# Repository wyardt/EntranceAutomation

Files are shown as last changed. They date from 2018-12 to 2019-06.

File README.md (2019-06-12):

# EntranceAutomation

This is the original use case:
### for the guest
When the guest arrives, he/she should enter the door number of the host by the keyboard and then the bell in the host's house will ring. After the identity of the visitor is confirmed using the phone of the system, the host presses the bottom and then the locked door downstairs will be open. Then the visitor can walk in.
### for the host
When the host needs to go out or come back home, he/she has to use a RF key to open the door.
### for the administator
Remote manage all the RF keys, including enable the key or disable it.

## TARGET
And my target is remake the subsystem in my house in order to control it remotely for the first step and then to make all this automatic which I don't have to 

## Detailed Needs
Below is the original goals, but it seems that it's impossible to mock the knock action from the subsystem inside the house because even though we can generate the signal which should be from the downstairs, the state of the system downstairs do will stay the same and just won't react to the unlock action from my subsystem.

~~1. Control it inside the house~~

~~* Hack the original system~~

~~* Automated open~~

~~* Automated open only once when the control switch is turned on~~

~~2. Control it from local internet web page~~

~~3. Control it from internet web page~~

~~4. Control it on my phone~~

~~5. Control it automately depending on my position~~

so here is the compromising targets:(under the scenario that somebody or I have just enter my door number and the bell is ringring)
1. Unlock the door using a single button
2. Unlock the door through my computer wirelessly
3. Unlock the door automately whoever visits
4. Unlock the door automately only once since a button has been pressed
5. Unlock the door through a web page which is post to the internet
6. Unlock the door from APP
7. Unlock the door automately depending on my position

## Hace the subsystem
First take a look at of how the system works at the normal situation. 
1. When someone enters the door number, the phone rings. If phone is picked up and unlock key is pressed, the door downstairs will be unlocked, if nobody answers, after about twenty seconds, the phone stops ringing and even then the phone is picked up and press the unlock key, there won't be any effect. So there is a time window for us to take the decision of whether unlock the door or not.
2. If nobody enters the door number, press the unlock key inside the house, there won't be any actions taken place. So we couldn't simply unlock the door downstairs whenever we want.
3. Pick up the phone inside the house, there is nothing can be heard from the line. So some mechanic blocks the voice signal when nobody visits. 

Then disassembling the subsystem[TODO image]and it turns out to be that the main chip on the subsystem is HT12D which is a serial decoder. And it could be inferred from the PCB and the frame that the top-left switch(“SW_Hook” for short below) is for the pick up action and the one(“SW_Unlock” for short below) on the right-bottom is the unlock action which is exactly the same with the print.

So here is the simplest way to hack this subsystem. On one hand, add an additional path for each of the two switches, then the control logic could be taken over by any MCU that is responsible for it. On the other hand, monitor the signal from outside the subsystem or monitor the control logic signal inside the subsystem, then the MCU could takes over the control logic inside the right time window.

So the simplest way of control the subsystem is monitor D0 and once it becomes active, enable the SW_Hook first, and then enable the SW_Unlock, so the door downstairs shall be unlocked. And more option could be added after detecting the D0 is active, such as remote notation and remote control and so on.

# More Information 
Below is the debugging and some trying with the HT12D chip which does little help of implementing the goals that mentioned. But if you are interested of the chip's function just for your information.

From datasheet of HT12D and HT12E, when someone visits, device downstairs will launch the knocking by sending:
    [sync head(12x"000" and 1x"001" )] [A0-A7][D0-D3]
which in total 13 data signals. And "001" represents '1', "011" is '0'.

For HT12D, if 3 out of 4 times of code matched, VT output high(which is not used in this subsystem), D0-D3 will be latched(D0 is used as the control signal in this subsystem), till Din is no longer active.

address set on board is 0101 1011 as it could be seen from PCB:
<div align=center>
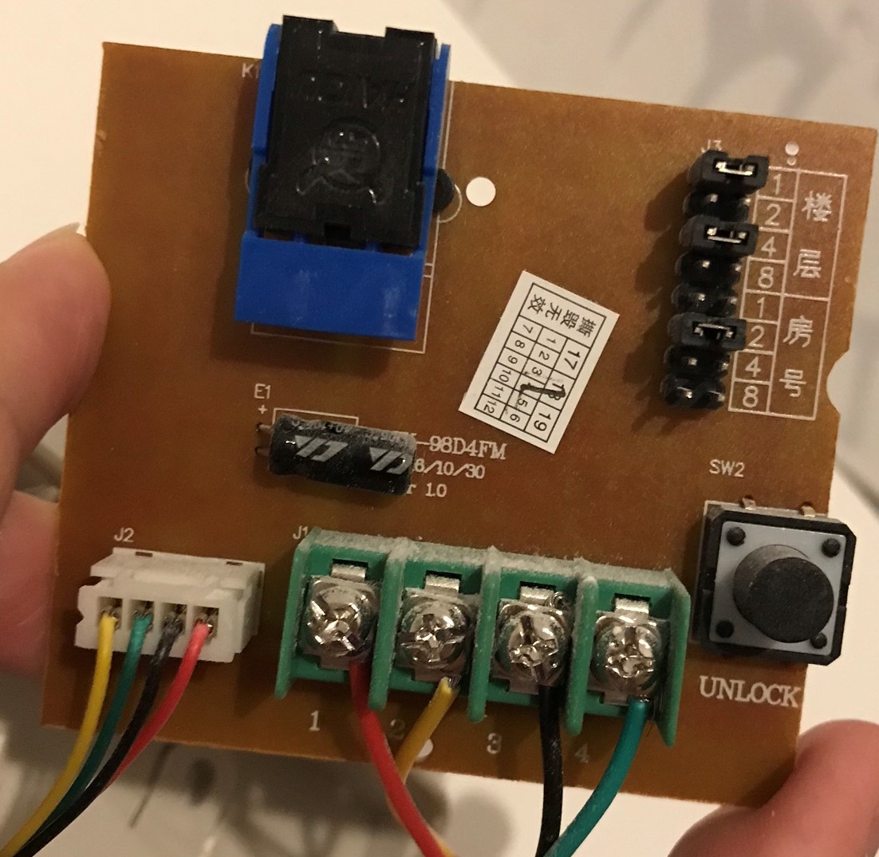
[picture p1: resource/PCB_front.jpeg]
address setting on PCB


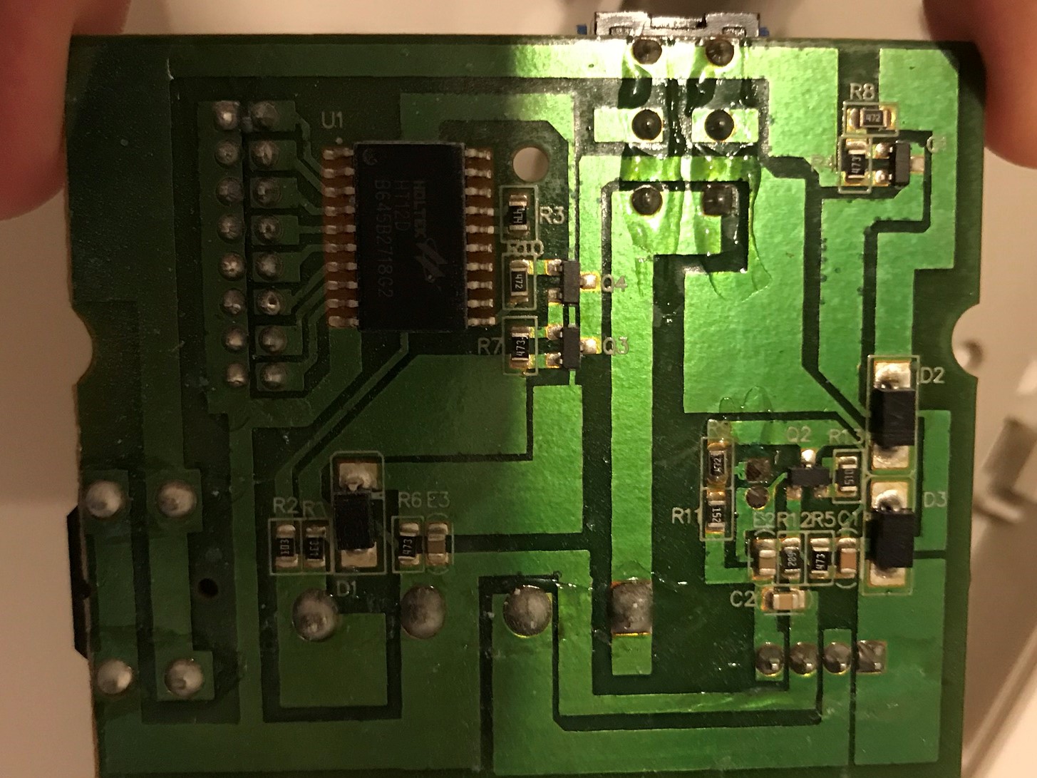
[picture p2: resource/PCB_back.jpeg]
address setting on PC

</div>

wave measured is:
1(guiding code) 0101 1011 1100 as it could be seen from oscilloscope:
<div align=center>
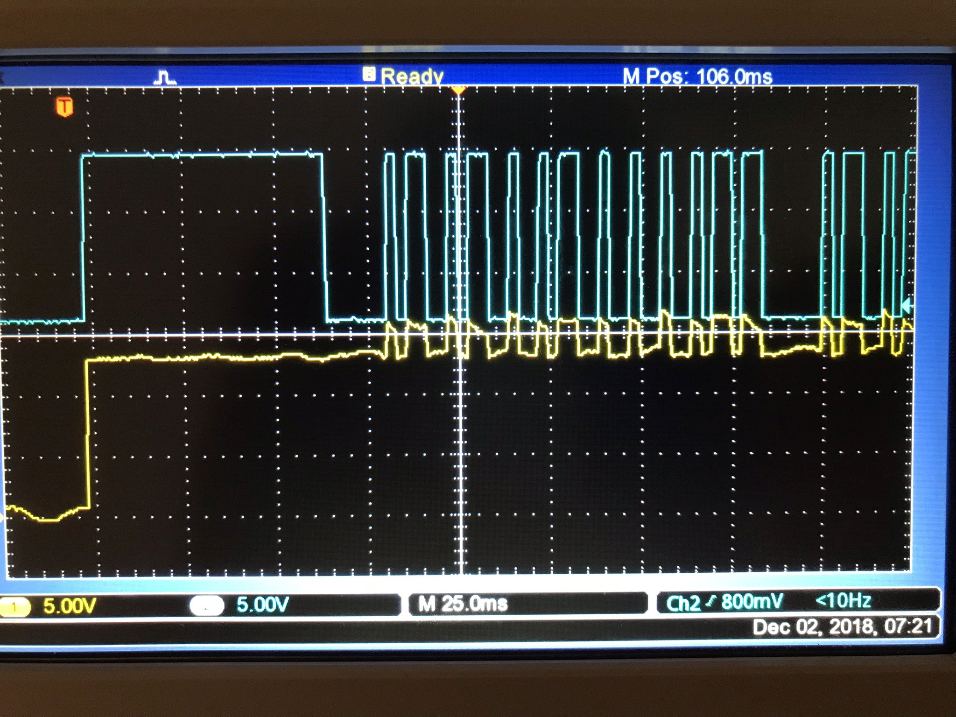
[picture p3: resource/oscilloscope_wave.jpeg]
someone knock on 502 door

</div>
and my door number is 502 so it's matched correctly.

And here is a way of decoding the knocking signal on the MCU:
record the 1.5 times the width of the sync head and use it as the mark. when the width of the upcoming signal is less than the mark, a '1' is received otherwise is a '0'.
And of course if we have another HT12D then we could emit this procedure by just monitoring the D0 signal of this HT12D chip.

# Hardware Scheme
What we have now is the subsystem itself, and we plan to take control of the two main control switches of the subsystem and what's more we don't want to modify the original functions of the subsystem, which is to say that, we could use the subsystem as what it used to be after even we have modified the subsystem by our will.

For the sake of simplicity, We choose to use modules which are off the rack. All we have to do is to redirect the control pathes onto a SPDT and use a MCU to decide which input should appear on the control path.

From the figure below it's the sketch of the modification. On the left side is the original path of the two switches, on the right side is the modification scheme.(S2 is a MUX of 2, default state is connect 3 to 2 which makes the path is the same with the original scheme)
Here we use a N-channel power MOSFET as the switch which is on when grid is positive.
<div align=center>
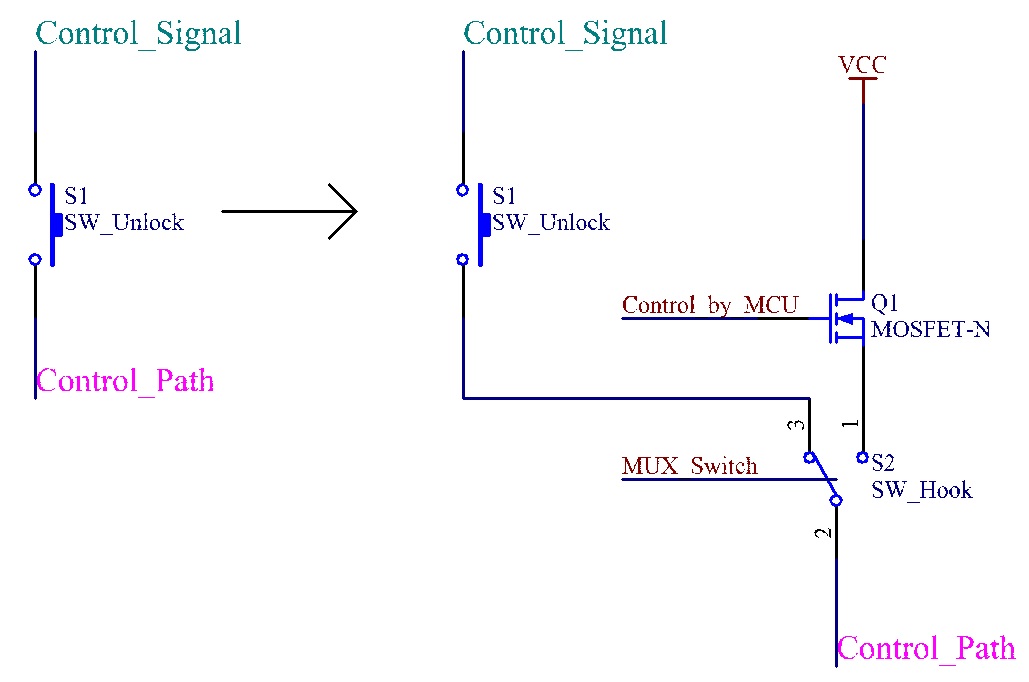
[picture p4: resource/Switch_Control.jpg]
switch_modification

</div>

Wait a minute, we have another scheme that omits the SPDT and it seems better. Look at the picture below.
<div align=center>
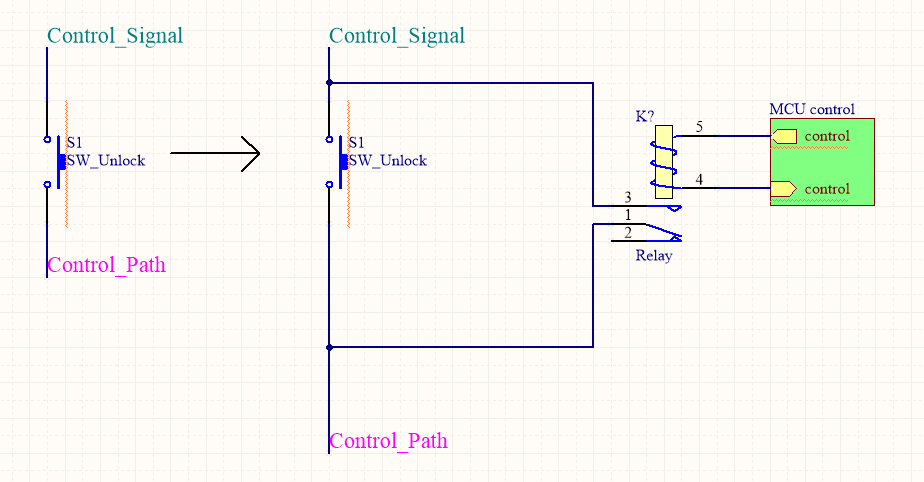
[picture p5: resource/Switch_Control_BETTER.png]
switch_modification

</div>

So this modification goes with the SW_Hook and the SW_Unlock (OR and the D0 signal path, see note below).

NOTE: for the monitor of someone visits, disconnect the D0 signal and connect it to MCU, and make the D0 signal path stay active all the time(which makes we can hear the talking all the time).(This is reserved for furthur experiment because it seems that when D0 signal path is always active, the system would be unable to function when someone enter any the door number, if this is confirmed, we can only monitor this signal and just leave it alone)

MCU we choose the STM8S103F module which is cost effective and easy to use.

What is said above are the overall modules we use with this scheme.

# Software Scheme
All we have to do is to control the MOSFET and the MUX when the D0 is detected active.
So here is the scheme of unlock the door with a single button:
1. Monitor the D0 of HT12D, if D0 is active, enable the SW_Hook control signal and go to 2, otherwise return to 1.
2. If Test Key is pressed, enable the SW_Unlock control signal and go to 3, otherwise stay in 2.
3. Wait until D0 is no longer active and go to 1, otherwise stay in 3.

Then varies functions can be deprived from the scheme above, such as control it through my computer or my mobile phone, so before all that might happen, let's build it up bit by bit.

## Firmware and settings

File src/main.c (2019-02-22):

/**
  ******************************************************************************
  * @file    Project/main.c 
  * @author  MCD Application Team
  * @version V2.1.0
  * @date    18-November-2011
  * @brief   Main program body
  ******************************************************************************
  * @attention
  *
  * THE PRESENT FIRMWARE WHICH IS FOR GUIDANCE ONLY AIMS AT PROVIDING CUSTOMERS
  * WITH CODING INFORMATION REGARDING THEIR PRODUCTS IN ORDER FOR THEM TO SAVE
  * TIME. AS A RESULT, STMICROELECTRONICS SHALL NOT BE HELD LIABLE FOR ANY
  * DIRECT, INDIRECT OR CONSEQUENTIAL DAMAGES WITH RESPECT TO ANY CLAIMS ARISING
  * FROM THE CONTENT OF SUCH FIRMWARE AND/OR THE USE MADE BY CUSTOMERS OF THE
  * CODING INFORMATION CONTAINED HEREIN IN CONNECTION WITH THEIR PRODUCTS.
  *
  * <h2><center>&copy; COPYRIGHT 2011 STMicroelectronics</center></h2>
  ******************************************************************************
  */ 


/* Includes ------------------------------------------------------------------*/
#include "stm8s.h"
#include "main.h"

bool someone_is_knocking = FALSE;
bool automate_unlock_once = FALSE;

/* Private defines -----------------------------------------------------------*/
/* Private function prototypes -----------------------------------------------*/
/* Private functions ---------------------------------------------------------*/
static void CLK_Config(void);
static void GPIO_Config(void);
static void Flash_LED(uint16_t flash_times);
static void TurnOff_LED(void);

void Delay(uint16_t nCount)
{
  /* Decrement nCount value */
  while (nCount != 0)
  {   
    nCount--;
  }
}
void main(void)
{
	disableInterrupts();

	/* Clock configuration -----------------------------------------*/
	CLK_Config();

	/* GPIO Configuration ---------------------------------------*/
  GPIO_Config();
  /* Initialize the Interrupt sensitivity */
  EXTI_SetExtIntSensitivity(EXTI_PORT_GPIOA, EXTI_SENSITIVITY_RISE_ONLY);
  EXTI_SetTLISensitivity(EXTI_TLISENSITIVITY_RISE_ONLY);
  
  enableInterrupts();

  Flash_LED(10);
  TurnOff_LED();
  wfi();
  
  while (1)
  {
  	/* if (automate_unlock_once == TRUE) */ /* under any condition */
  	{
  		automate_unlock_once = FALSE;
  		
	    if (someone_is_knocking == TRUE)
	    {
	    	Flash_LED(50);
	    	GPIO_WriteHigh(PICKUP_GPIO_PORT, PICKUP_GPIO_PINS);	/* pick up */
				Flash_LED(20);
				GPIO_WriteHigh(UNLOCK_GPIO_PORT, UNLOCK_GPIO_PINS);	/* open the gate */
				Flash_LED(20);
				GPIO_WriteLow(UNLOCK_GPIO_PORT, UNLOCK_GPIO_PINS);	/* release the button */
				Flash_LED(20);
				GPIO_WriteLow(PICKUP_GPIO_PORT, PICKUP_GPIO_PINS);	/* automate hang up */
				someone_is_knocking = FALSE;	/* open gate complete */
				Flash_LED(5);
	    }
	  }
          wfi();
  }
  
}

/**
  * @brief  Configure system clock to run at 16Mhz, default is 2MHz after reset
  * @param  None
  * @retval None
  */
static void CLK_Config(void)
{
    /* Initialization of the clock */
    /* Clock divider to HSI/1 */
    CLK_HSIPrescalerConfig(CLK_PRESCALER_HSIDIV2);
}

/**
  * @brief  Configure GPIO for buttons and Leds available on the evaluation board
  * @param  None
  * @retval None
  */
static void GPIO_Config(void)
{
  /* Initialize I/Os in Output Mode for LEDs */
	GPIO_Init(LED_GPIO_PORT, LED_GPIO_PINS, GPIO_MODE_OUT_PP_LOW_FAST);

	/* Initialize I/Os in Output Mode for control signals */
	GPIO_Init(PICKUP_GPIO_PORT, PICKUP_GPIO_PINS, GPIO_MODE_OUT_PP_LOW_FAST);
	GPIO_Init(UNLOCK_GPIO_PORT, UNLOCK_GPIO_PINS, GPIO_MODE_OUT_PP_LOW_FAST);

	/* Initialize I/Os in Input Mode for local control button */
	GPIO_Init(LOCAL_BUTTON_GPIO_PORT, LOCAL_BUTTON_GPIO_PINS, GPIO_MODE_IN_FL_IT);
	
  /* Initialize I/O in Input Mode with Interrupt for knocking signal detect */
  GPIO_Init(KNOCK_GPIO_PORT, KNOCK_GPIO_PINS, GPIO_MODE_IN_FL_IT);

	GPIO_WriteLow(PICKUP_GPIO_PORT, PICKUP_GPIO_PINS);	/* default state is hooked */
  GPIO_WriteLow(UNLOCK_GPIO_PORT, UNLOCK_GPIO_PINS);	/* default is no action to open the gate */
}

/**
  * @brief  Flash the LED to indicate process is run here
  * @param  None
  * @retval None
  */
static void Flash_LED(uint16_t flash_times)
{
  uint16_t i;
	/* LED flashes to indicate successful initiation */
  for (i = 0; i < flash_times; i++)
  {
		GPIO_WriteReverse(LED_GPIO_PORT, LED_GPIO_PINS);
		Delay(0xffff);
  }

}

/**
  * @brief  Turn off the LED
  * @param  None
  * @retval None
  */
static void TurnOff_LED(void)
{
	GPIO_WriteHigh(LED_GPIO_PORT, LED_GPIO_PINS);
}

#ifdef USE_FULL_ASSERT

/**
  * @brief  Reports the name of the source file and the source line number
  *   where the assert_param error has occurred.
  * @param file: pointer to the source file name
  * @param line: assert_param error line source number
  * @retval : None
  */
void assert_failed(u8* file, u32 line)
{ 
  /* User can add his own implementation to report the file name and line number,
     ex: printf("Wrong parameters value: file %s on line %d\r\n", file, line) */

  /* Infinite loop */
  while (1)
  {
  }
}
#endif

/******************* (C) COPYRIGHT 2011 STMicroelectronics *****END OF FILE****/

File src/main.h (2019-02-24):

/**
  ******************************************************************************
  * @file    EXTI_InterruptPriority\main.h
  * @author  MCD Application Team
  * @version V2.0.4
  * @date    26-April-2018
  * @brief   This file contains the external declaration for main.c file.
  ******************************************************************************
  * @attention
  *
  * <h2><center>&copy; COPYRIGHT 2014 STMicroelectronics</center></h2>
  *
  * Licensed under MCD-ST Liberty SW License Agreement V2, (the "License");
  * You may not use this file except in compliance with the License.
  * You may obtain a copy of the License at:
  *
  *        http://www.st.com/software_license_agreement_liberty_v2
  *
  * Unless required by applicable law or agreed to in writing, software 
  * distributed under the License is distributed on an "AS IS" BASIS, 
  * WITHOUT WARRANTIES OR CONDITIONS OF ANY KIND, either express or implied.
  * See the License for the specific language governing permissions and
  * limitations under the License.
  *
  ******************************************************************************
  */   

/* Define to prevent recursive inclusion -------------------------------------*/
#ifndef __MAIN_H
#define __MAIN_H

/* Private typedef -----------------------------------------------------------*/
/* Private define ------------------------------------------------------------*/
#define LED_GPIO_PORT  (GPIOB)
#define LED_GPIO_PINS  (GPIO_PIN_5)
#define KNOCK_GPIO_PORT  (GPIOA)
#define KNOCK_GPIO_PINS  (GPIO_PIN_1)
#define PICKUP_GPIO_PORT  (GPIOA)
#define PICKUP_GPIO_PINS  (GPIO_PIN_2)
#define UNLOCK_GPIO_PORT  (GPIOD)
#define UNLOCK_GPIO_PINS  (GPIO_PIN_4)
#define LOCAL_BUTTON_GPIO_PORT  (GPIOD)
#define LOCAL_BUTTON_GPIO_PINS  (GPIO_PIN_5)



/* Private function prototypes -----------------------------------------------*/
/* Private functions ---------------------------------------------------------*/

/* Public functions ----------------------------------------------------------*/
extern bool someone_is_knocking;
extern bool automate_unlock_once;

#endif /* __MAIN_H */


/************************ (C) COPYRIGHT STMicroelectronics *****END OF FILE****/

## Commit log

2018-12-10 add Switch Control sketch
2018-12-11 Add AD scheme of switch path upgrade
    [Switch_Control.SchDoc]
2018-12-11 Modify Switch_Control.jpg
2018-12-11 add gitignore and move AD files to resource folder
    [Switch_Control.SchDoc]
2018-12-15 Use a better scheme of switch control side path
    [Switch_Control.SchDoc]
2019-01-20 add en.stsw-stm8069.zip which contains the stm8s10x standard peripheral driver
2019-01-23 use "!= RESET" instead of "== SET" when determine interrupt IOs
    [main.c, main.h, stm8s_it.c]
2019-02-16 switch pickup key and unlock key add delay before pickup succeed of automate unlock the gate
2019-02-22 modify the better hardware scheme
    [Switch_Control.SchDoc]
2019-02-24 replace PICKUP_GPIO_PINS and UNLOCK_GPIO_PINS to meet the actual hardware
    [main.h]
